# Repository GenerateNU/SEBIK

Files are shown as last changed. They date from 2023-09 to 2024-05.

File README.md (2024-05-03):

# SEBIK
The software portion of the safety subsystem will mostly deal with less critical errors as it is assumed that there is still communication between the microcontroller and its peripherals. The main software safety feature exists in the heating state. As the code runs through the state machine every 10 milliseconds or so, it checks if we must switch the band heater on or off based on two conditions. Are we at or above our optimal plastic melting temperature and have we heated at that optimal temperature for the full duration required to melt the pellets. 

Since, this is a software safety feature, there is a chance that it can fail in case we get stuck in some infinite loop due to an edge case or our microcontroller becomes unresponsive. A watchdog timer was used in the main state machine so it could reset the microcontroller in case any of these happened.

The band heater is allowed to operate for 4 minutes as some time is needed to reach the 165°C required to melt the PP. and 3.5 minutes is required for the band heater to completely melt all the PP within the barrel before moving to the next state. 

To do so, the code employs a timer that is initialized at the beginning of the Heating State. This conditional allows the heater to count the amount of time the band heater has been operating at the proper temperature. A watchdog timer will only run when the heater is at an optimal state and count until it reaches 4 minutes of heating time. In real time, this causes the process to run for longer than 4 minutes, however, this is necessary to ensure all the PP is melted.

## Directory Structure:
```
.
|
|───production  # contains files needed for final prototype
|   |
|   |───sebik-eCAD    # contains the KiCAD project
|   └───sebik-src     # contains the code needed for deployment
|
|───testing     # contains files relevant to testing components
|
└───README.md   # this file!
```

## Practice Good Git Hygiene!
1. Only commit files you intended to change
2. Create branches for each feature, and larger branches for each development effort (i.e. ```develop/*```)
3. Check your branch before starting work
4. Pull frequently to avoid conflicts
5. Make Pull Requests when you are ready to merge into a larger branch

## Git Resources

* [Setting up Git](https://fanatical-colossus-434.notion.site/Git-Installation-and-Setup-d07b7d1ab5544424876f9fd3b4a0b312)
* [Intro to Git Crash Course](https://fanatical-colossus-434.notion.site/Crash-Course-Intro-to-Git-809641611da9478b8f9cca8fd97e49fe)

## EE Resources

* [Intro to KiCAD](https://fanatical-colossus-434.notion.site/EE-Crashcourse-Using-Kicad-To-Design-Schematics-8c7091b07237425bae66616ad1f77371)
* [EE Crash Course](https://fanatical-colossus-434.notion.site/EE-Crash-Course-Hardware-2023-c0c7cd5b55cf401e87f8b6c2c8c84336)

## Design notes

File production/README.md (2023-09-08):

# Production
This directory is for code/schematics/layouts that will be implemented in the final prototype.

> **_NOTE:_** If you have code to test out a component/subsystem, it should probably go into ```/testing```

## Directory Structure:
```
.
|───autopasser-ecad    # contains any schematic/board development files
|
└───autopasser-src     # contains any embedded code or important scripts
```

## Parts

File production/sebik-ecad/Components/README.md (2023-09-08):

This is where relevant KiCAD components are stored

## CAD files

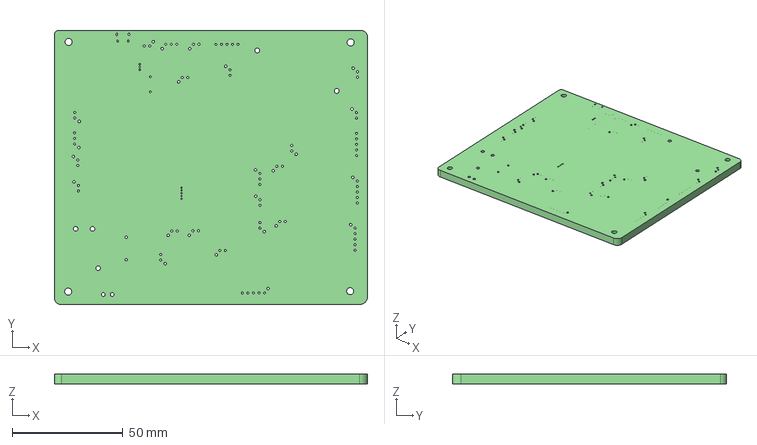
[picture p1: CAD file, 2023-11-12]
production/sebik-ecad/Sebik_mainboard/Sebik_mainboard.step
141.4 x 123.8 x 4.69 mm

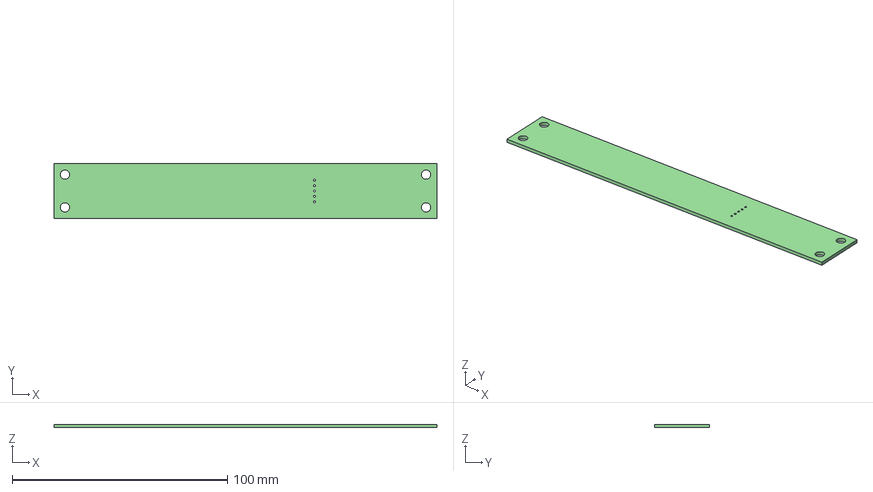
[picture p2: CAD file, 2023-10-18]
production/sebik-ecad/LEDBoard/LEDBoard/LEDBoard.step
177.8 x 25.4 x 1.60 mm

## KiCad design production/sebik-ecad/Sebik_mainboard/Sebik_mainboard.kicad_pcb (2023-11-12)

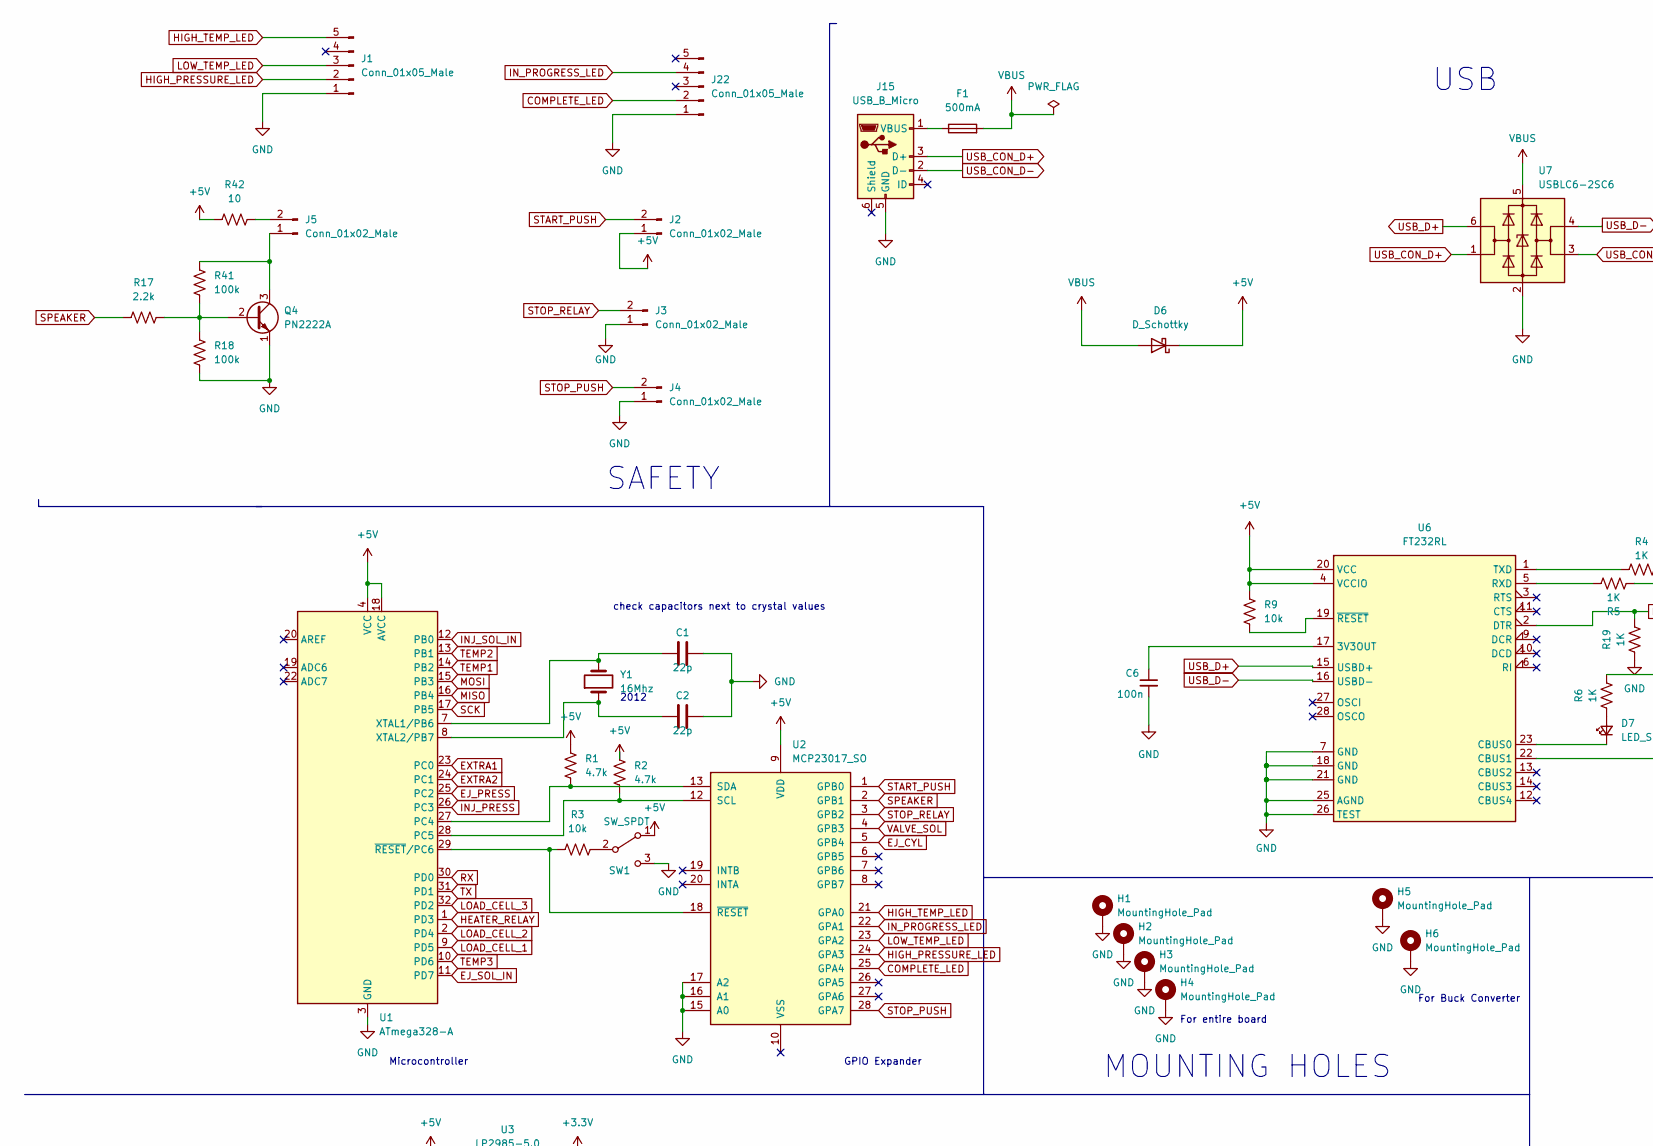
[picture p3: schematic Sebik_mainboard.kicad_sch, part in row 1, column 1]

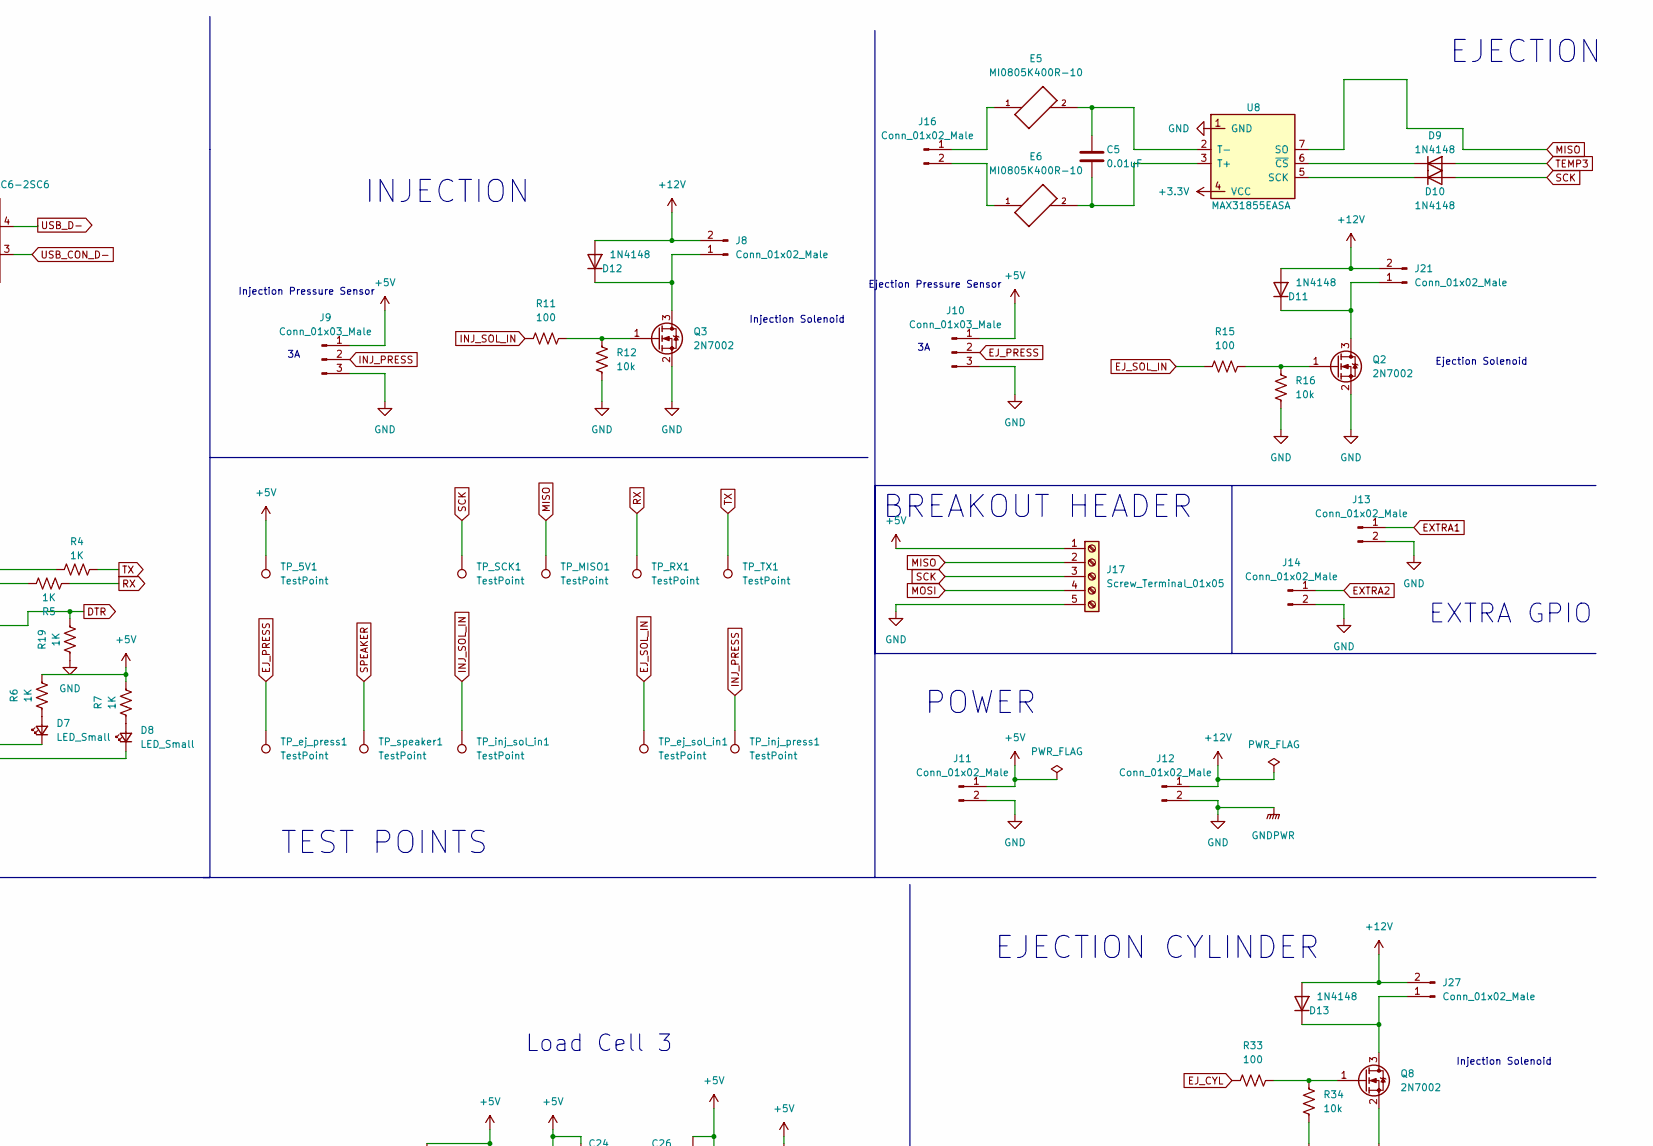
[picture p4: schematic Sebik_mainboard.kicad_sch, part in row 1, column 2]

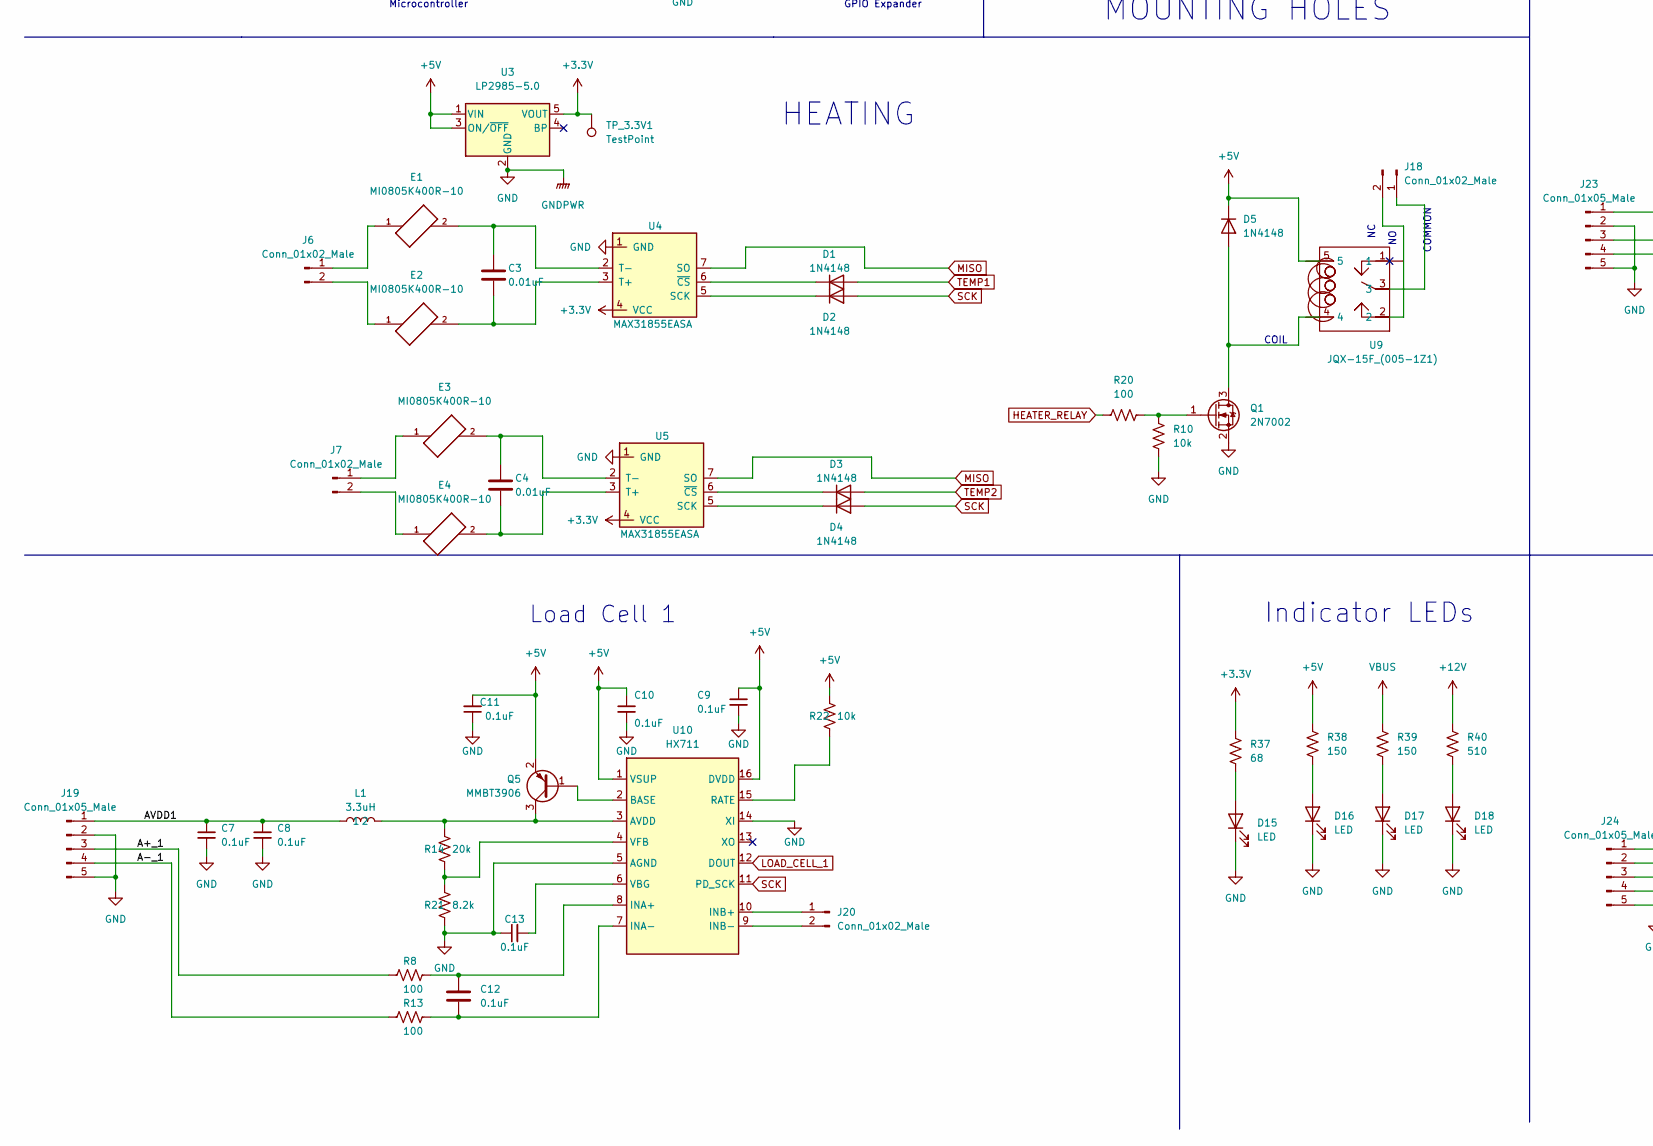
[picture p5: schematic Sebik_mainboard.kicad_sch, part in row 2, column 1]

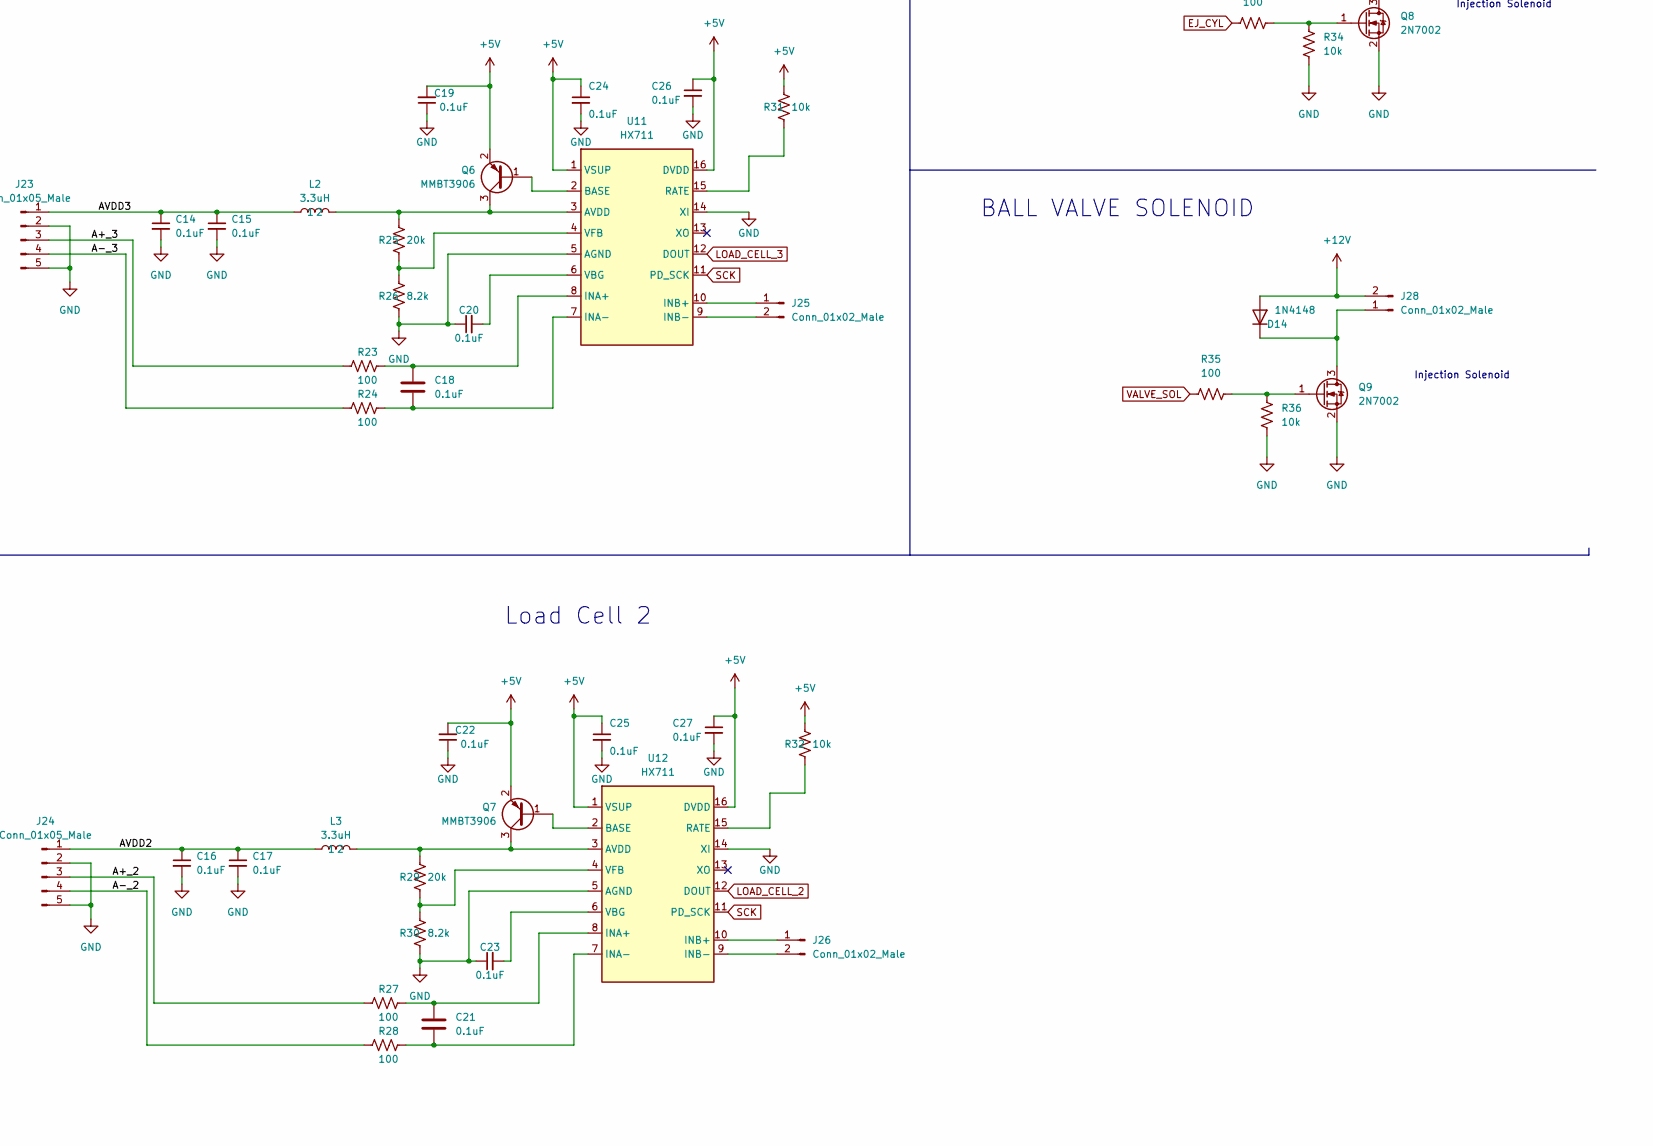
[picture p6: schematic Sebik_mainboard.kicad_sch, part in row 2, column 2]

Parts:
C1, C2: 22p; C_0805_2012Metric
C3, C4, C5: 0.01uF; C_0805_2012Metric
C6: 100n; C_0805_2012Metric
C7, C8, C9, C10, C11, C12, C13, C14, C15, C16, C17, C18, C19, C20, C21, C22, C23, C24, C25, C26, C27: 0.1uF; C_0805_2012Metric
D1, D2, D3, D4, D5, D9, D10, D11, D12, D13, D14: 1N4148; D_0805_2012Metric
D6: D_Schottky; D_0805_2012Metric
D7, D8: LED_Small; LED_0805_2012Metric
D15, D16, D17, D18: LED; LED_0805_2012Metric
E1, E2, E3, E4, E5, E6: MI0805K400R-10; C_0805_2012Metric
F1: 500mA; Fuse_1210_3225Metric
H1, H2, H3, H4: MountingHole_Pad; MountingHole_3.2mm_M3_DIN965_Pad
H5, H6: MountingHole_Pad; MountingHole_2.2mm_M2_DIN965_Pad
J1, J22: Conn_01x05_Male; JST_XH_B5B-XH-A_1x05_P2.50mm_Vertical
J2, J3, J4, J5, J6, J7, J8, J11, J12, J13, J14, J16, J20, J21, J25, J26, J27, J28: Conn_01x02_Male; JST_XH_B2B-XH-AM_1x02_P2.50mm_Vertical
J9, J10: Conn_01x03_Male; JST_XH_B3B-XH-AM_1x03_P2.50mm_Vertical
J15: USB_B_Micro; USB_Micro-B_Amphenol_10103594-0001LF_Horizontal
J17: Screw_Terminal_01x05; PinHeader_1x05_P1.27mm_Vertical
J18: Conn_01x02_Male; JST_VH_B2P-VH-B_1x02_P3.96mm_Vertical
J19, J23, J24: Conn_01x05_Male; JST_XH_B5B-XH-AM_1x05_P2.50mm_Vertical
L1, L2, L3: 3.3uH; L_0805_2012Metric
Q1, Q2, Q3, Q8, Q9: 2N7002; SOT-23
Q4: PN2222A; TO-92_Inline
Q5, Q6, Q7: MMBT3906; SOT-23
R1, R2: 4.7k; R_0805_2012Metric
R3, R9, R10, R12, R16, R22, R31, R32, R34, R36: 10k; R_0805_2012Metric
R4, R5, R6, R7, R19: 1K; R_0805_2012Metric
R8, R11, R13, R15, R20, R23, R24, R27, R28, R33, R35: 100; R_0805_2012Metric
R14, R25, R29: 20k; R_0805_2012Metric
R17: 2.2k; R_0805_2012Metric
R18, R41: 100k; R_0805_2012Metric
R21, R26, R30: 8.2k; R_0805_2012Metric
R37: 68; R_0805_2012Metric
R38, R39: 150; R_0805_2012Metric
R40: 510; R_0805_2012Metric
R42: 10; R_0805_2012Metric
SW1: SW_SPDT; SW_SPDT_CK-JS102011SAQN
TP_3.3V1, TP_5V1: TestPoint; TestPoint_Pad_D1.5mm
TP_MISO1: TestPoint; TestPoint_Pad_D1.5mm
TP_RX1: TestPoint; TestPoint_Pad_D1.5mm
TP_SCK1: TestPoint; TestPoint_Pad_D1.5mm
TP_TX1: TestPoint; TestPoint_Pad_D1.5mm
TP_ej_press1: TestPoint; TestPoint_Pad_D1.5mm
TP_ej_sol_in1: TestPoint; TestPoint_Pad_D1.5mm
TP_inj_press1: TestPoint; TestPoint_Pad_D1.5mm
TP_inj_sol_in1: TestPoint; TestPoint_Pad_D1.5mm
TP_speaker1: TestPoint; TestPoint_Pad_D1.5mm
U1: ATmega328-A; TQFP-32_7x7mm_P0.8mm
U2: MCP23017_SO; SOIC-28W_7.5x17.9mm_P1.27mm
U3: LP2985-5.0; SOT-23-5
U4, U5, U8: MAX31855EASA; SOIC-8_3.9x4.9mm_P1.27mm
U6: FT232RL; SSOP-28_5.3x10.2mm_P0.65mm
U7: USBLC6-2SC6; SOT-23-6
U9: JQX-15F_(005-1Z1); JQX-15F(005-181) (1)
U10, U11, U12: HX711; SOP-16_3.9x9.9mm_P1.27mm
Y1: 16Mhz; Crystal_SMD_2520-4Pin_2.5x2.0mm

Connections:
+3.3V: R37.1, TP_3.3V1.1, U3.5 (VOUT), U4.4 (VCC), U5.4 (VCC), U8.4 (VCC)
+12V: D11.2 (A), D12.2 (A), D13.2 (A), D14.2 (A), J8.2, J12.1, J21.2, J27.2, J28.2, R40.1
/A+_1: J19.3, R8.2
/A+_2: J24.3, R27.2
/A+_3: J23.3, R23.2
/A-_1: J19.4, R13.2
/A-_2: J24.4, R28.2
/A-_3: J23.4, R24.2
/AVDD1: C7.1, C8.1, J19.1, L1.1
/AVDD2: C16.1, C17.1, J24.1, L3.1
/AVDD3: C14.1, C15.1, J23.1, L2.1
DTR: R19.2, U6.2 (DTR)
EJ_CYL: R33.2, U2.5 (GPB4)
EJ_PRESS: J10.2, TP_ej_press1.1, U1.25 (PC2)
EJ_SOL_IN: R15.1, TP_ej_sol_in1.1, U1.11 (PD7)
EXTRA1: J13.1, U1.23 (PC0)
EXTRA2: J14.1, U1.24 (PC1)
HEATER_RELAY: R20.1, U1.1 (PD3)
HIGH_PRESSURE_LED: J1.2, U2.24 (GPA3)
HIGH_TEMP_LED: J1.5, U2.21 (GPA0)
INJ_SOL_IN: R11.2, TP_inj_sol_in1.1, U1.12 (PB0)
IN_PROGRESS_LED: J22.4, U2.22 (GPA1); also elsewhere on the board
LOAD_CELL_1: U1.9 (PD5), U10.12 (DOUT)
LOAD_CELL_2: U1.2 (PD4), U12.12 (DOUT)
LOAD_CELL_3: U1.32 (PD2), U11.12 (DOUT)
LOW_TEMP_LED: J1.3, U2.23 (GPA2)
MISO: J17.2, TP_MISO1.1, U1.16 (PB4), U4.7 (SO), U5.7 (SO), U8.7 (SO)
MOSI: J17.4, U1.15 (PB3)
unnamed: C1.1, U1.7 (XTAL1/PB6), Y1.2
unnamed: C2.1, U1.8 (XTAL2/PB7), Y1.1
unnamed: C3.1, E1.2, U4.2 (T-)
unnamed: C3.2, E2.2, U4.3 (T+)
unnamed: C4.1, E3.2, U5.2 (T-)
unnamed: C4.2, E4.2, U5.3 (T+)
unnamed: C5.1, E5.2, U8.2 (T-)
unnamed: C5.2, E6.2, U8.3 (T+)
unnamed: C6.1, U6.17 (3V3OUT)
unnamed: C12.1, R8.1, U10.8 (INA+)
unnamed: C12.2, R13.1, U10.7 (INA-)
unnamed: C13.2, U10.6 (VBG)
unnamed: C18.1, R23.1, U11.8 (INA+)
unnamed: C18.2, R24.1, U11.7 (INA-)
unnamed: C20.2, U11.6 (VBG)
unnamed: C21.1, R27.1, U12.8 (INA+)
unnamed: C21.2, R28.1, U12.7 (INA-)
unnamed: C23.2, U12.6 (VBG)
unnamed: D1.1 (K), U4.6 (~CS)
unnamed: D2.1 (K), U4.5 (SCK)
unnamed: D3.1 (K), U5.6 (~CS)
unnamed: D4.1 (K), U5.5 (SCK)
unnamed: D5.2 (A), Q1.3 (D), U9.4
unnamed: D7.1 (K), U6.23 (CBUS0)
unnamed: D7.2 (A), R6.1
unnamed: D8.1 (K), U6.22 (CBUS1)
unnamed: D8.2 (A), R7.1
unnamed: D9.1 (K), U8.6 (~CS)
unnamed: D10.1 (K), U8.5 (SCK)
unnamed: D11.1 (K), J21.1, Q2.3 (D)
unnamed: D12.1 (K), J8.1, Q3.3 (D)
unnamed: D13.1 (K), J27.1, Q8.3 (D)
unnamed: D14.1 (K), J28.1, Q9.3 (D)
unnamed: D15.2 (A), R37.2
unnamed: D16.2 (A), R38.2
unnamed: D17.2 (A), R39.2
unnamed: D18.2 (A), R40.2
unnamed: E1.1, J6.1
unnamed: E2.1, J6.2
unnamed: E3.1, J7.1
unnamed: E4.1, J7.2
unnamed: E5.1, J16.1
unnamed: E6.1, J16.2
unnamed: F1.1, J15.1 (VBUS)
unnamed: J5.1, Q4.3 (C), R41.2
unnamed: J5.2, R42.2
unnamed: J18.1, U9.3
unnamed: J18.2, U9.2
unnamed: J20.1, U10.10 (INB+)
unnamed: J20.2, U10.9 (INB-)
unnamed: J25.1, U11.10 (INB+)
unnamed: J25.2, U11.9 (INB-)
unnamed: J26.1, U12.10 (INB+)
unnamed: J26.2, U12.9 (INB-)
unnamed: L1.2, Q5.3 (C), R14.1, U10.3 (AVDD)
unnamed: L2.2, Q6.3 (C), R25.1, U11.3 (AVDD)
unnamed: L3.2, Q7.3 (C), R29.1, U12.3 (AVDD)
unnamed: Q1.1 (G), R10.2, R20.2
unnamed: Q2.1 (G), R15.2, R16.2
unnamed: Q3.1 (G), R11.1, R12.2
unnamed: Q4.2 (B), R17.2, R18.2, R41.1
unnamed: Q5.1 (B), U10.2 (BASE)
unnamed: Q6.1 (B), U11.2 (BASE)
unnamed: Q7.1 (B), U12.2 (BASE)
unnamed: Q8.1 (G), R33.1, R34.2
unnamed: Q9.1 (G), R35.1, R36.2
unnamed: R1.2, U1.27 (PC4), U2.13 (SDA)
unnamed: R2.2, U1.28 (PC5), U2.12 (SCL)
unnamed: R3.1, SW1.2 (B)
unnamed: R3.2, U1.29 (~RESET/PC6), U2.18 (~RESET)
unnamed: R4.2, U6.1 (TXD)
unnamed: R5.2, U6.5 (RXD)
unnamed: R9.1, U6.19 (~RESET)
unnamed: R14.2, R21.1, U10.4 (VFB)
unnamed: R22.2, U10.15 (RATE)
unnamed: R25.2, R26.1, U11.4 (VFB)
unnamed: R29.2, R30.1, U12.4 (VFB)
unnamed: R31.2, U11.15 (RATE)
unnamed: R32.2, U12.15 (RATE)
RX: R5.1, TP_RX1.1, U1.30 (PD0)
SCK: D2.2 (A), D4.2 (A), D10.2 (A), J17.3, TP_SCK1.1, U1.17 (PB5), U10.11 (PD_SCK), U11.11 (PD_SCK), U12.11 (PD_SCK)
SPEAKER: R17.1, TP_speaker1.1, U2.2 (GPB1)
START_PUSH: J2.2, U2.1 (GPB0)
STOP_PUSH: J4.2, U2.28 (GPA7)
STOP_RELAY: J3.2, U2.3 (GPB2)
TEMP1: D1.2 (A), U1.14 (PB2)
TEMP2: D3.2 (A), U1.13 (PB1)
TEMP3: D9.2 (A), U1.10 (PD6)
TX: R4.1, TP_TX1.1, U1.31 (PD1)
USB_CON_D+: J15.3 (D+), U7.1 (I/O1)
USB_CON_D-: J15.2 (D-), U7.3 (I/O2)
USB_D+: U6.15 (USBD+), U7.6 (I/O1)
USB_D-: U6.16 (USBD-), U7.4 (I/O2)
VALVE_SOL: R35.2, U2.4 (GPB3)
VBUS: D6.2 (A), F1.2, R39.1, U7.5 (VBUS)

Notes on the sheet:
Injection Solenoid
check capacitors next to crystal values
BREAKOUT HEADER
MOUNTING HOLES
EXTRA GPIO
For Buck Converter
For entire board
Indicator LEDs
COIL
HEATING
POWER
Load Cell 2
BALL VALVE SOLENOID
Injection Pressure Sensor
Load Cell 3
2012
EJECTION CYLINDER
GPIO Expander
EJECTION
TEST POINTS
Microcontroller
Ejection Solenoid
SAFETY
USB
COMMON
Ejection Pressure Sensor
INJECTION
Load Cell 1

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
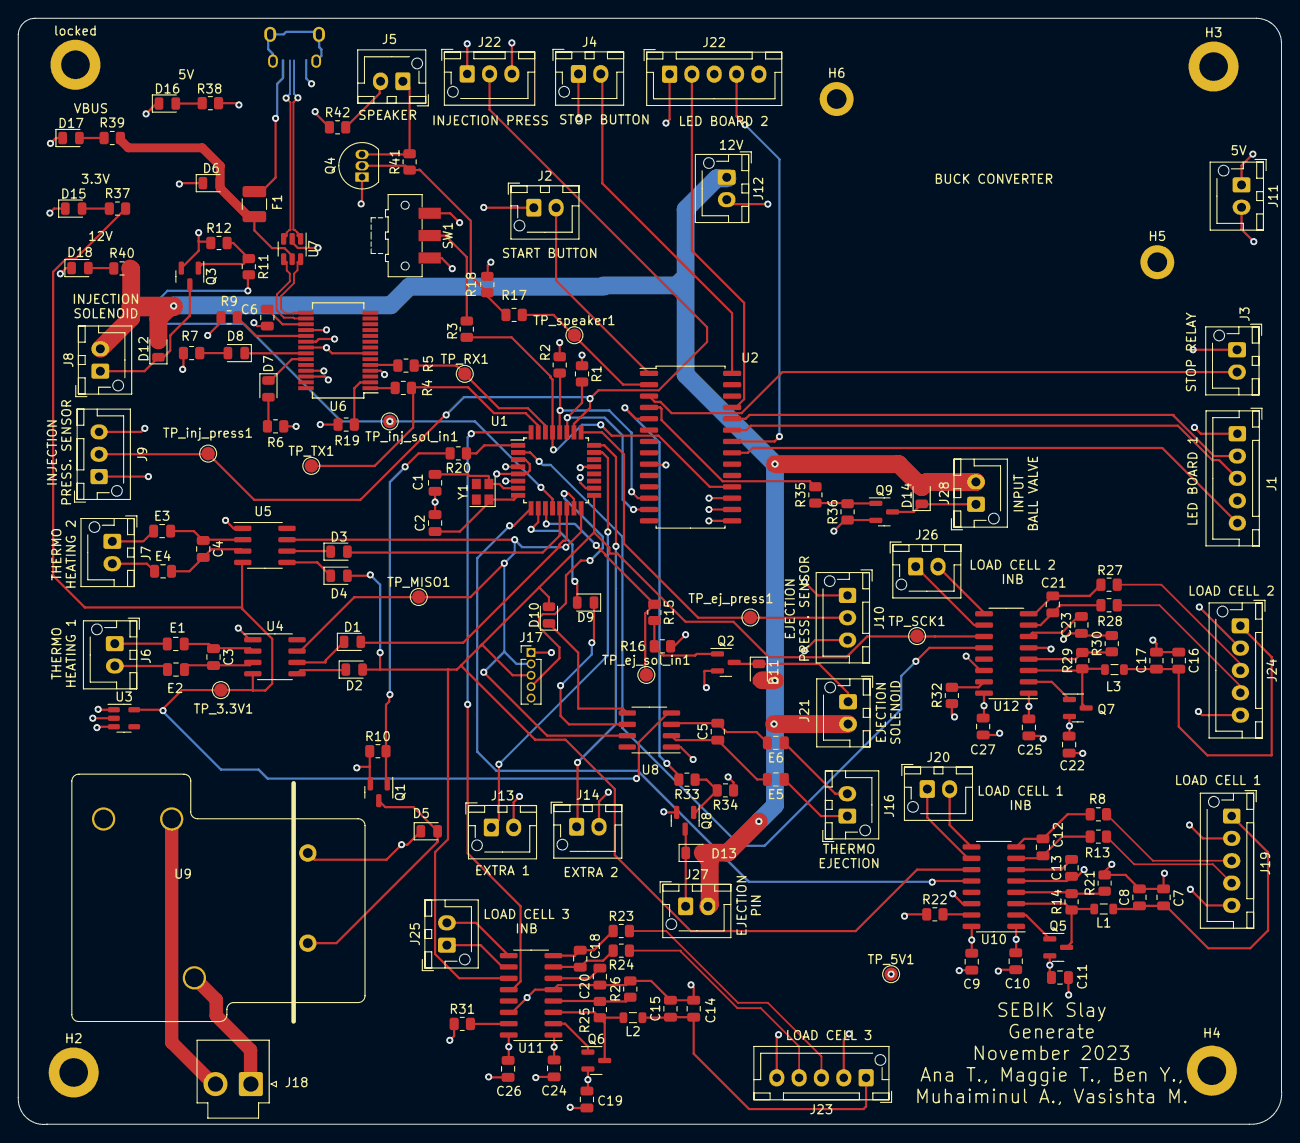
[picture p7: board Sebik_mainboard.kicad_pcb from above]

Board: 4 copper layers, 141.4 x 123.8 mm, 166 parts (1 on the bottom side), 127 nets.

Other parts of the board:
J22#2: Conn_01x05_Male; JST_XH_B5B-XH-A_1x05_P2.50mm_Vertical
locked: MountingHole_Pad; MountingHole_3.2mm_M3_DIN965_Pad

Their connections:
IN_PROGRESS_LED: J22#2.4; also elsewhere on the board

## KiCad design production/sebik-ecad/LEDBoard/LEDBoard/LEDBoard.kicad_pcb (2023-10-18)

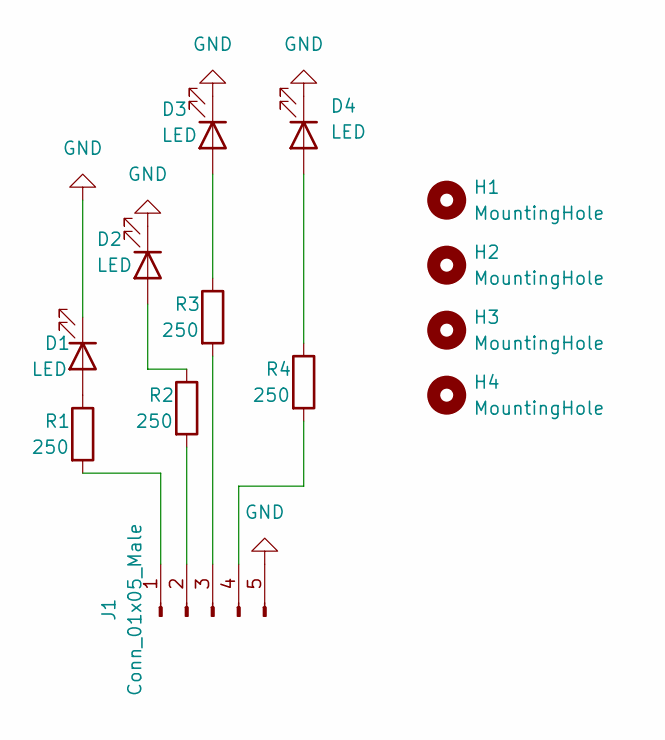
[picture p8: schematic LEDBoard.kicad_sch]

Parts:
D1, D2, D3, D4: LED; LED_0805_2012Metric
H1, H2, H3, H4: MountingHole; MountingHole_4.3mm_M4
J1: Conn_01x05_Male; JST_XH_B5B-XH-A_1x05_P2.50mm_Vertical
R1, R2, R3, R4: 250; LED_0805_2012Metric

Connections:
GND: D1.1 (K), D2.1 (K), D3.1 (K), D4.1 (K), J1.5
unnamed: D1.2 (A), R1.1
unnamed: D2.2 (A), R2.1
unnamed: D3.2 (A), R3.1
unnamed: D4.2 (A), R4.1
unnamed: J1.1, R1.2
unnamed: J1.2, R2.2
unnamed: J1.3, R3.2
unnamed: J1.4, R4.2

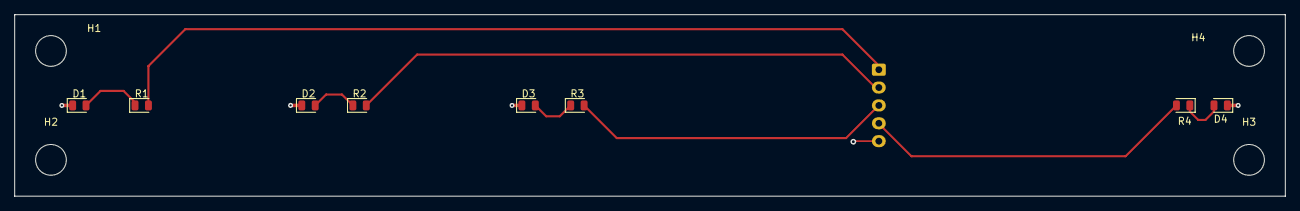
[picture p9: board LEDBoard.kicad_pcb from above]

Board: 2 copper layers, 177.8 x 25.4 mm, 13 parts (1 on the bottom side), 9 nets.

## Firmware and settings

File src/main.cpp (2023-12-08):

#include <Arduino.h>
#include <avr/wdt.h>
#include <Adafruit_MCP23X17.h>
#include <Adafruit_MAX31855.h>
#include "StateMachine.hpp"

#define BAUD_RATE 115200

// Crystal Oscillator
//#define F_CPU 16000000UL

// Watchdog timer
#define WATCHDOG_TIMEOUT WDTO_8S

Adafruit_MCP23X17 gpioExpander;


StateMachineHandler stateMachineHandler(gpioExpander);

void setup()
{   
    stateMachineHandler.InitializePins();
    wdt_disable();
    delay(3000);
    wdt_enable(WATCHDOG_TIMEOUT);

    Serial.begin(9600);
    gpioExpander.begin_I2C();
    stateMachineHandler.StartStateMachine();
}

void loop()
{
    stateMachineHandler.MainStateMachine();
    wdt_reset();
}

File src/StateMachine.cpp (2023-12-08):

#include "StateMachine.hpp"

HX711_ADC load_cell_1(LOAD_CELL_SENSOR1, SCK);
HX711_ADC load_cell_2(LOAD_CELL_SENSOR2, SCK);
HX711_ADC load_cell_3(LOAD_CELL_SENSOR3, SCK);

Adafruit_MAX31855 thermocouple1(SCK, TEMP_SENSOR1, MISO);
Adafruit_MAX31855 thermocouple2(SCK, TEMP_SENSOR2, MISO);
Adafruit_MAX31855 thermocouple3(SCK, TEMP_SENSOR3, MISO);

StateMachineHandler::StateMachineHandler(Adafruit_MCP23X17 expander)
{
    gpioExpander = expander;
}

StateMachineHandler::~StateMachineHandler()
{
}

// Main state machine
void StateMachineHandler::MainStateMachine()
{
    switch(m_currentState)
    {
        case START:
            Start();
            break;
        case CLAMPING:
            Clamping();
            break;
        case PLASTIC_DISPENSES:
            PlasticDispense();
            break;
        case HEATING:
            Heating();
            break;
        case INJECTING:
            Injecting();
            break;
        case EJECTING:
            Unclamping();
            break;
        case FINSHED:
            Finish();
            break;
        default:
            break;
    }
    delay(10);
}

// Updates the current state
void StateMachineHandler::Update(States state)
{
    m_currentState = state;
}

void StateMachineHandler::InitializePins()
{
    //NOTE: TEMPORARILY MADE ALL PINS OUTPUT FOR HARDWARE TESTING
    // GPIO expander pinmodes
    gpioExpander.pinMode(START_PUSHBUTTON_E, OUTPUT);
    gpioExpander.pinMode(SPEAKER_E, OUTPUT);
    gpioExpander.pinMode(HIGH_TEMP_LED_E, OUTPUT);
    gpioExpander.pinMode(IN_PROGRESS_LED_E, OUTPUT);
    gpioExpander.pinMode(LOW_TEMP_LED_E, OUTPUT);
    gpioExpander.pinMode(HIGH_PRESSURE_LED_E, OUTPUT);
    gpioExpander.pinMode(COMPLETE_LED_E, OUTPUT);
    gpioExpander.pinMode(BALL_VALVE_SOLENOID_E, OUTPUT);
    gpioExpander.pinMode(EJECTION_CYLINDER_SOLENOID_E, OUTPUT);
    //gpioExpander.pinMode(HARD_STOP_RELAY_E, OUTPUT);

    pinMode(INJECTION_SOLENOID, OUTPUT);
    pinMode(EJECTION_SOLENOID, OUTPUT);
    pinMode(MISO, OUTPUT);
    pinMode(MOSI, OUTPUT);
    pinMode(SCK, OUTPUT);
    pinMode(TEMP_SENSOR1, OUTPUT);
    pinMode(TEMP_SENSOR2, OUTPUT);
    pinMode(TEMP_SENSOR3, OUTPUT);
    pinMode(INJECTION_SENSOR, OUTPUT);
    pinMode(EJECTION_SENSOR, OUTPUT);
    pinMode(LOAD_CELL_SENSOR1, OUTPUT);
    pinMode(LOAD_CELL_SENSOR2, OUTPUT);
    pinMode(LOAD_CELL_SENSOR3, OUTPUT);
    pinMode(HEATER_RELAY, OUTPUT);
    pinMode(AIR_PUMP_RELAY, OUTPUT);
    pinMode(EXTRA2, OUTPUT);

    load_cell_1.setCalFactor(809.03);
    load_cell_2.setCalFactor(836.88);
    load_cell_3.setCalFactor(771.25);
}

// Triggers state machine
void StateMachineHandler::StartStateMachine()
{
    Update(States::START);
}

// Executes start procedure
void StateMachineHandler::Start()
{
    if (IsStartButtonPressed())
    {
        InProgressLEDOn();
        PlaySpeaker();
        Update(States::CLAMPING);
    }
}

// Executes clamping procedure
void StateMachineHandler::Clamping()
{
    delay(300);
    digitalWrite(EJECTION_SOLENOID, LOW);
    m_previous_weight = GetTotalHopperWeight(); // weight before plastic is dispensed: hopper and plastic
    Update(States::PLASTIC_DISPENSES);
}

// Executes the plastic dispensing procedure
void StateMachineHandler::PlasticDispense()
{
    float curr_weight = GetTotalHopperWeight();

    // Calculates the plastic dispensed by keeping track of the previous and current weight
    if (m_plastic_dispensed >= PETRI_DISH_WEIGHT) 
    {
        gpioExpander.digitalWrite(BALL_VALVE_SOLENOID_E, LOW);
        Update(States::HEATING);
        m_plastic_dispensed = m_plastic_dispensed - PETRI_DISH_WEIGHT;
    }
    else 
    {
        gpioExpander.digitalWrite(BALL_VALVE_SOLENOID_E, HIGH);
        m_plastic_dispensed = m_plastic_dispensed + m_previous_weight - curr_weight;
        m_previous_weight = curr_weight;
    }
}

// Gets the current hopper weight
float StateMachineHandler::GetTotalHopperWeight()
{
    return load_cell_1.getData() + load_cell_2.getData() + load_cell_3.getData();
}

// Executes the heating procedure
void StateMachineHandler::Heating()
{
    // PLastic must be heated at optimal temp for 4 min
    if (m_timeHeated <= 240000)
    {
        int heatingStartTime = millis();
        if (GetTempReading(thermocouple1) >= OPTIMAL_TEMP_IN_CELSIUS)
        {
            // turn heater off
            int heatingOptimalTempTime = millis();
            m_timeHeated = m_timeHeated + heatingOptimalTempTime - heatingStartTime;
            digitalWrite(HEATER_RELAY, LOW);
        }
        else
        {
            digitalWrite(HEATER_RELAY, HIGH);
        }
    }
    else
    {
        m_timeHeated = 0;
        Update(States::INJECTING);
    }
}

// Executes the injecting procedure
void StateMachineHandler::Injecting()
{
if (IsPressureHandled(INJECTION_SENSOR))
    {
        digitalWrite(INJECTION_SOLENOID, HIGH);
        Update(States::EJECTING);
    }
}

// Executes the unclamping procedure
void StateMachineHandler::Unclamping()
{
    if (IsPressureHandled(EJECTION_SENSOR))
    {
            //injection cylinder
            digitalWrite(INJECTION_SOLENOID, LOW);
            delay(1000);
            //ejection cylinder
            digitalWrite(EJECTION_SOLENOID, LOW);
            //some kind of timer
            delay(1000);
            //mini little air cylinder
            digitalWrite(EJECTION_CYLINDER_SOLENOID_E, HIGH);
            Update(States::FINSHED);
    }
}

// Executes the finish procedure
void StateMachineHandler::Finish()
{
    digitalWrite(EJECTION_CYLINDER_SOLENOID_E, LOW);
    if (IsPlasticSafeToTouch())
    {
        CompleteLEDOn();
        delay(1000);
        CompleteLEDOff();
        Update(States::CLAMPING);
    }
}

// Gets the temperature reading from the supplied thermocouple
double StateMachineHandler::GetTempReading(Adafruit_MAX31855 thermocouple)
{
    thermocouple.begin();
    return thermocouple.readCelsius();
}

// Returns if the plastic in the ejection drawer is safe to touch
bool StateMachineHandler::IsPlasticSafeToTouch()
{
    return GetTempReading(thermocouple3) < SAFE_TEMP_TO_TOUCH_IN_CELSIUS;
}

// Gets the pressure reading from the supplied pressure sensor pin
float StateMachineHandler::GetPressureReading(int pin) 
{
    float currentPressureValue = analogRead(pin);
    currentPressureValue = currentPressureValue / 1000;
    return currentPressureValue;
}

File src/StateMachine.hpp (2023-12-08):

#ifndef STATEMACHINE_HPP
#define STATEMACHINE_HPP

#include <HX711_ADC.h>
#include <Adafruit_MCP23X17.h>
#include <Adafruit_MAX31855.h>

// UI pins
#define START_PUSHBUTTON_E 1
#define SPEAKER_E 2
#define HIGH_TEMP_LED_E 21
#define IN_PROGRESS_LED_E 22
#define LOW_TEMP_LED_E 23
#define HIGH_PRESSURE_LED_E 24
#define COMPLETE_LED_E 25
//#define HARD_STOP_BUTTON_E 7

// Solenoid pins
#define INJECTION_SOLENOID 12
#define EJECTION_SOLENOID 11
#define BALL_VALVE_SOLENOID_E 4
#define EJECTION_CYLINDER_SOLENOID_E 5

// SPI
#define MISO 16
#define MOSI 15
#define SCK 17

// Sensor pins
#define TEMP_SENSOR1 14
#define TEMP_SENSOR2 13
#define TEMP_SENSOR3 10
#define INJECTION_SENSOR 26
#define EJECTION_SENSOR 25
#define LOAD_CELL_SENSOR1 9
#define LOAD_CELL_SENSOR2 2
#define LOAD_CELL_SENSOR3 32

// Relays
#define HEATER_RELAY 1
#define AIR_PUMP_RELAY 23 // Used to be EXTRA1

#define EXTRA2 24

const int HIGH_TEMP_IN_CELSIUS = 175;
const int OPTIMAL_TEMP_IN_CELSIUS = 165;

const int SAFE_TEMP_TO_TOUCH_IN_CELSIUS = 40;

const int HIGH_PRESSURE_IN_PSI = 100;
const int OPTIMAL_PRESSURE_IN_PSI = 90; 
const int LOW_PRESSURE_IN_PSI = 80;

const float PETRI_DISH_WEIGHT = 100; // g, change this later to actual weight

const float calibration_factor = 199900; //-7050 worked for my 440lb max scale setup

enum States
{
    START,
    CLAMPING,
    PLASTIC_DISPENSES,
    HEATING,
    INJECTING,
    EJECTING,
    FINSHED,
    HARD_STOP
};

class StateMachineHandler
{
    private:
        enum States m_currentState;
        int m_timeHeated = 0; 
        float m_plastic_dispensed = 0;
        float m_previous_weight;
        Adafruit_MCP23X17 gpioExpander;

    public:
        StateMachineHandler(Adafruit_MCP23X17 expander);

        ~StateMachineHandler();

        void InitializePins();

        void StartStateMachine();

        // Updates the current state
        void Update(States state);

        // Triggers state machine

        // Main state machine
        void MainStateMachine();

        // Executes start procedure
        void Start();

        // Executes clamping procedure
        void Clamping();

        // Executes the plastic dispensing procedure
        void PlasticDispense();

        // Gets the current hopper weight
        float GetTotalHopperWeight();

        // Executes the heating procedure
        void Heating();

        // Executes the injecting procedure
        void Injecting();

        // Executes the unclamping procedure
        void Unclamping();

        // Executes the finish procedure
        void Finish();

        // Gets the pressure reading from the supplied pressure sensor pin
        float GetPressureReading(int pin);

        // Gets the temperature reading from the supplied thermocouple
        double GetTempReading(Adafruit_MAX31855 thermocouple);

        // Returns if the plastic in the ejection drawer is safe to touch
        bool IsPlasticSafeToTouch();

        void HardwareTest();

        bool IsStartButtonPressed();

        void PlaySpeaker();

        void HighTempLEDOn();
        
        void HighTempLEDOff();

        void LowTempLEDOn();

        void LowTempLEDOff();

        void HighPressureLEDOn();

        void HighPressureLEDOff();

        void InProgressLEDOn();

        void InProgressLEDOff();

        void CompleteLEDOn();

        void CompleteLEDOff();

        bool IsPressureHandled(int pin);
};

#endif

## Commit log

2023-10-18 Committing the current file for main schematic and PCB and LED board schematic and PCB
    [LEDBoard.kicad_pcb, LEDBoard.kicad_sch, LEDBoard.step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]
2023-10-19 updated schematic with usb port, test points, and mounting holes
    [SEBIK_R1.kicad_pcb, SEBIK_R1.kicad_sch]
2023-10-19 added non power net test points, numbered all parts and added crystal and switch footprints
    [SEBIK_R1.kicad_sch]
2023-10-23 added mounting holes for buck converter and connector for 5v from buck
    [SEBIK_R1.kicad_sch]
2023-10-23 added connector for relay to shut down power
    [SEBIK_R1.kicad_sch]
2023-10-23 changed microUSB to USBC
    [SEBIK_R1.kicad_sch]
2023-10-23 took off pulldown resistors on thermocouple sensors
    [SEBIK_R1.kicad_sch]
2023-11-12 adding last version of PCB- sent to fabrication
    [LEDBoard.kicad_sch, Sebik_mainboard.kicad_pcb, Sebik_mainboard.kicad_sch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]
2023-11-12 Updates for matching pins, watchdog timer, testing hardware
2023-11-16 Low Pressure Error Handling
    [StateMachine.cpp, StateMachine.hpp]
2023-11-19 Heating changes added.
2023-11-19 Heating changes 0.2
2023-11-19 Heating changes 0.3:
2023-11-21 Updated Pressure Sensor Code
